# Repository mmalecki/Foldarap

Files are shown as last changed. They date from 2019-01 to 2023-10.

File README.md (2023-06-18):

The Swoon, a folding RepRap
============================

The Swoon is a fork of [Emmanuel Gilloz's Foldarap](https://github.com/EmmanuelG/Foldarap), aimed at upgrading
it with a new motion system based on belts and linear rails, as well as making it compatible with the [EVA 3.0 carriage platform](https://main.eva-3d.page/).

The original SketchUp CAD model has mostly been recreated in [OpenSCAD](https://openscad.org/).

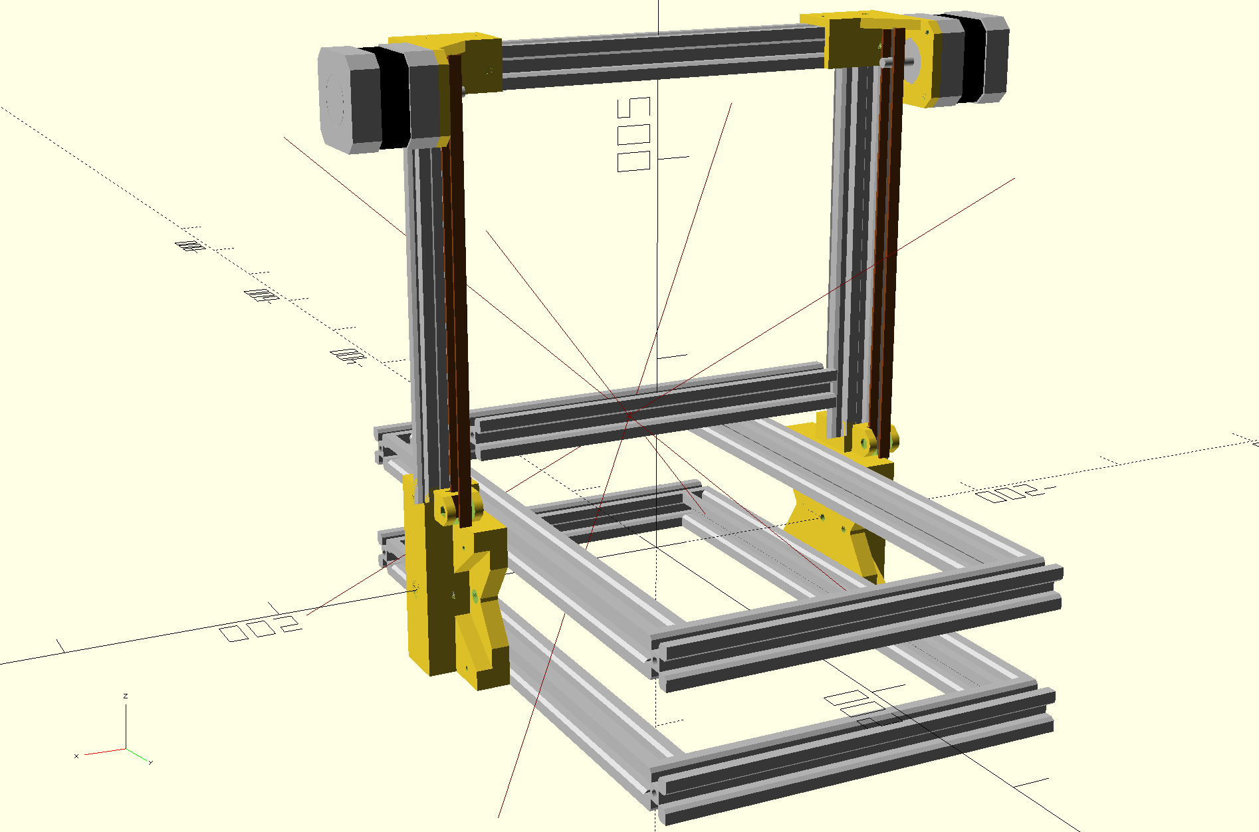
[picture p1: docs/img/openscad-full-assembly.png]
OpenSCAD assembly


This project is still heavily WIP. Belted Z has been implemented, with the rest coming shortly.

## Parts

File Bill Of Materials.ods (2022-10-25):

T (alim ext) | U |  |  | Total | Base |  |  | Y-axis |  |  |  |  | Electronics |  |  | Z-axis |  |  | X-axis |  |  |  |  | Spool roller
662.1 | 473.88 | Exemple Link | Item F 4.0 | 332.6 | Chassis | Hinges | Panels | Y-endstop | Y-idler | Y-slider | Y-motor | Plate | Rear plate | Front plate | Board | Chassis | Z-motor | Handle | Extruder | X-motor | X-endstop | Fan | Hot-end
45 | 25 | Motedis (http://www.motedis.com/shop/Friends-of/FoldaRap-v30/Kit-FoldaRap-v30::5729.html) | V-slot aluminium profile 2020 200mm | 6 | 4 |  |  |  |  |  |  |  |  |  |  | 1 |  |  |  | 1
 |  |  | V-slot aluminium profile 2020 300mm | 6 | 4 |  |  |  |  |  |  |  |  |  |  | 2
 |  |  | M4 T-nut | 62 | 16 | 6 | 4 | 1 | 1 |  | 2 |  | 8 | 4 |  | 10 | 4 | 2 |  | 4
 |  |  | GT2 6mm 600mm timing belt (1m) | 1 |  |  |  |  |  | 1
 |  |  | GT2 20 teeth, 5mm bore timing pulley | 1 |  |  |  |  |  |  | 1
15 | 1 | Kipp (https://www.kipp.fr/fr/fr/Produits/Eléments-de-manœuvre-Eléments-normalisés/Poussoirs-à-ressort-doigt-d-indexage-broches-à-billes/K0334-Poussoirs-à-ressort-mo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) | Ball spring plunger - Kipp K0334.210 | 8 |  | 8
20 | 10 | Fix-n-vis | M3n | 4 |  |  |  |  |  |  |  |  |  |  |  |  | 2 |  |  |  |  |  | 2
 |  | Fix-n-vis | M3n wing | 3 |  |  |  |  |  |  |  | 3
 |  | Fix-n-vis | M3nN | 8 |  |  |  |  | 1 | 4 |  | 3
 |  | Fix-n-vis | M3 washer | 1 |  |  |  |  | 1
 |  | Fix-n-vis | M3x6 headless | 5 |  |  |  |  |  |  |  |  |  |  |  |  |  |  |  | 5
 |  |  | M2.5x12 | 8
 |  | Fix-n-vis | M3x8 CHC | 10 |  |  |  |  |  |  |  |  |  |  | 4 |  | 4 |  |  | 2
 |  | Fix-n-vis | M3x10 CHC | 9 |  |  |  |  |  | 4 | 4 |  |  |  |  |  |  |  | 1
 |  | Fix-n-vis | M3x20 CHC | 1 |  |  |  |  | 1
 |  | Fix-n-vis | M3x25 CHC | 4 |  |  |  |  |  |  |  |  |  |  |  |  |  |  | 4
 |  | Fix-n-vis | M3x30 TFHC | 11 |  |  |  |  |  |  |  | 3 |  |  |  |  | 4 |  |  | 2 |  |  | 2
 |  | Fix-n-vis | M4x8 TBHC | 52 | 16 | 6 | 4 | 1 | 1 |  | 2 |  | 8 |  |  | 10 |  | 2 |  | 2
 |  | Fix-n-vis | M4x10 TBHC | 10 |  |  |  |  |  |  |  |  |  | 4 |  |  | 4 |  |  | 2
 |  | Fix-n-vis | M4x25 CHC | 2 |  | 2
 |  | Fix-n-vis | M4nN | 2 |  | 2
 |  | Fix-n-vis | M4 medium washer | 4 |  | 4
 |  |  | M2.5 heat set insert | 8 |  |  |  |  |  |  |  |  |  |  |  |  |  |  |  |  |  | 8
45 | 30 | e3d (https://e3d-online.com/lite6) | E3D Lite 6 HotEnd | 1 |  |  |  |  |  |  |  |  |  |  |  |  |  |  |  |  |  |  | 1
 |  | e3d (https://e3d-online.com/thermal-compound-paste) | Thermal compound paste | 0
 |  | e3D / RRW / Robotdigg | Filament drive gear (with grub screw) | 1 |  |  |  |  |  |  |  |  |  |  |  |  |  |  | 1
15 | 9 | metalaladecoupe (http://www.metalaladecoupe.com/francais/toles.asp?tbout=alu) | 150 x 140 x 4 mm aluminium plate | 1 |  |  |  |  |  |  |  | 1
30 | 20 | printbite (https://flex3drive.com/product/printbite/) | PrintBite 150 x 140 mm | 1 |  |  |  |  |  |  |  | 1
70 | 0.4 | Robotdigg (https://www.robotdigg.com/product/188/2pin-1M-Long-Thermistor-Cables-w/-Dupont-Connector) | 1 m 2-pin Dupont connector cable | 3 |  |  |  | 1 |  |  |  |  |  |  |  |  |  |  |  |  | 1 | 1
 | 0.6 | Robotdigg (https://www.robotdigg.com/product/141/Endstop-Subminiature-Switch-SS-5GL) | Mechanical endstop switch | 2 |  |  |  | 1 |  |  |  |  |  |  |  |  |  |  |  |  | 1
 | 6.6 | Robotdigg (https://www.robotdigg.com/product/7/NEMA17-40mm-long-17hs3001-20b-Stepper-Motor) | Nema17 – 40mm – 1.20A 4000gr – 50cm (240gr) | 4 |  |  |  |  |  |  | 1 |  |  |  |  |  | 2 |  | 1
 | 6.6 | Robotdigg (https://www.robotdigg.com/product/1034/Nema17-Pancake-Stepper-Motor) | Nema17 – 22mm – 0.8A 1200gr – 80cm (200gr) | 1 |  |  |  |  |  |  |  |  |  |  |  |  |  |  |  | 1
 |  | Robotdigg / Aliexpress | 90 W 100 x 100 m heating film with 100k thermistor and 2 pin molex connector | 1 |  |  |  |  |  |  |  | 1
 | 0.25 | Robotdigg (https://www.robotdigg.com/product/262/Ball-Bearing-603,-604) | 603ZZ bearing | 3 |  |  |  |  | 2 |  |  |  |  |  |  |  |  |  | 1
 | 0.3 | Robotdigg (https://www.robotdigg.com/product/12/608ZZ-Ball-Bearing) | 608ZZ bearing | 4 |  |  |  |  |  |  |  |  |  |  |  |  |  |  |  |  |  |  |  | 4
 |  | Robotdigg (https://www.robotdigg.com/product/249/PC4-01,-PC6-01,-PC4-M4,-PC6-M6-for-Bowden-Extruder) | PC4-B1 pneumatic fitting (4 mm tube, M6 thread) | 1 |  |  |  |  |  |  |  |  |  |  |  |  |  |  | 1
120 | 1.69 | RepRapWorld (https://reprapworld.com/products/cables_and_wiring/wires/heater_wire_yellow_1m_rated_5a/) | 18 AWG cable, green 250 mm | 1 |  |  |  |  |  |  |  |  | 1
 | 1.69 | RepRapWorld (https://reprapworld.com/products/cables_and_wiring/wires/heater_wire_red_1m_rated_5a/) | 18 AWG cable, red 250 + 100 mm | 1 |  |  |  |  |  |  |  |  | 1
 | 1.69 | RepRapWorld (https://reprapworld.com/products/cables_and_wiring/wires/heater_wire_black_1m_rated_5a/) | 18 AWG cable, black 250 + 100 mm | 1 |  |  |  |  |  |  |  |  | 1
 | 60 | RepRapWorld (https://reprapworld.com/products/electronics/minitronics/minitronics_v1_1_basic_kit/) | Minitronics + molex cable | 1 |  |  |  |  |  |  |  |  |  |  | 1
 | 5 | RepRapWorld (https://reprapworld.com/products/cables_and_wiring/wires/power_cable_1_8m/) | EU power cord | 1 |  |  |  |  |  |  |  |  | 1
 | 40 | RepRapWorld (https://reprapworld.fr/products/_lectronique/impression_autonome/_cran_graphique_lcd_v1_0/) | LCD écran pour Minitronics | 1 |  |  |  |  |  |  |  |  |  |  | 1
 | 2 | RepRapWorld (https://reprapworld.com/products/cables_and_wiring/cable_binding/cable_wrapping_10mm_1_meter/) | 1 m cable spiral wrap | 1.6 |  |  |  |  |  |  |  |  |  |  |  |  | 0.8 |  |  |  |  |  | 0.8
 | 3 | RepRapWorld (https://reprapworld.com/products/electronics/minitronics/usb_connection_cable_0_5m_type_b_to_type_a/) | USB cable | 1 |  |  |  |  |  |  |  |  |  |  | 1
 | 1.5 | RepRapWorld (https://reprapworld.com/products/cables_and_wiring/heatshrink/heatshrink_black_20cm_1_6mm_bore_0_8mm_shrunken/) | Heat shrink sleeve for the fans
40 | 1.32 | RS (http://fr.rs-online.com/web/p/products/0178462) | Zip ties | 7 |  |  |  |  |  | 5 |  |  |  | 2
 |  | RS (http://fr.rs-online.com/web/p/clips-de-maintient-de-cables/1705346/) | Cable clip 25x25x8m | 1 |  |  |  |  |  |  |  |  |  |  |  |  |  |  | 1
 | 1.72 | RS (http://fr.rs-online.com/web/p/gaine-thermoretractable-avec-adhesif/1706361/) | Heat shrink sleeve 1.6-0.8 mm 20 mm | 2 |  |  |  |  |  |  |  |  |  |  |  |  |  |  |  |  |  | 2
 | 0.03 | RS (http://fr.rs-online.com/web/p/embouts-de-cablage-a-sertir/2114268/) | Ferrule for the fans | 2 |  |  |  |  |  |  |  |  |  |  |  |  |  |  |  |  |  | 2
 | 1.89 | RS (http://fr.rs-online.com/web/p/gaine-thermoretractable-avec-adhesif/1706399/) | Heat shrink 4.8-2.4mm 20 mm | 4 |  |  |  | 2 |  |  |  |  |  |  |  |  |  |  |  |  | 2
 | 0.5 | RS (https://www.rs-particuliers.com/web/p/ressorts-de-compression/751483/) | 751-483 compression spring | 5 |  |  |  |  |  |  |  | 3 |  |  |  |  |  |  | 2
15 | 15 | Aliexpress / RS (https://fr.aliexpress.com/store/product/2-Pieces-Gdstime-12V-2Pin-3cm-30mm-x-30mm-x-10mm-Ball-Bearing-Brushless-DC-Cooling/212707_32797692869.html) | 30 x 30 x 10 mm fan (4.7 CFM) | 2 |  |  |  |  |  |  |  |  |  |  |  |  |  |  |  |  |  | 2
 |  | mouser (60) (https://www.mouser.fr/ProductDetail/MEAN-WELL/GST160A12-R7B/) | Meanwell 12 V 138 W (OEM / or not EU) external power supply
115 | 115 | RS (https://rs-particuliers.com/Product.aspx?Product=1176149) | Meanwell 12 V 138 W external power supply | 1 |  |  |  |  |  |  |  |  | 1
 |  | mouser (60) (https://www.mouser.fr/search/ProductDetail.aspx?R=0virtualkey0virtualkeyGST160A24-R7B) | Meanwell 24 V 160W (OEM / or not EU) external power supply
 |  | RS ? | Meanwell 24 V 160W external power supply
 |  | mouser (3) (https://www.mouser.fr/ProductDetail/Kycon/KPJX-PM-4S) | KPJX-PM-4S connector
7 | 7 | RS (https://rs-particuliers.com/Product.aspx?Product=6677287) | KPJX-PM-4S connector | 1 |  |  |  |  |  |  |  |  | 1
 |  | mouser (9) (https://www.mouser.fr/ProductDetail/Kycon/KPJX-PM-4S-S) | 8 mm drill or 90° reamer (alu plate)
0.1 | 0.1 | Fix-n-vis | M2.5x10 for plastic (? - play compensation ?) | 2 |  |  |  |  |  |  |  |  | 2
85 | 75 |  | PIECES 3D – PLA
 |  | silver | face-panel-A | 1 |  |  |  |  |  |  |  |  | 1
 |  | silver | face-panel-B-psu-external | 1 |  |  |  |  |  |  |  |  | 1
 |  | silver | side-panel-A | 2 |  |  | 2
 |  | navy | x-slider | 1 |  |  |  |  |  |  |  |  |  |  |  |  |  |  |  | 1
 |  | silver | y-carriage | 1 |  |  |  |  |  |  |  | 1
 |  | navy | y-slider-R | 1 |  |  |  |  |  | 1
 |  | navy | y-slider-L | 1 |  |  |  |  |  | 1
 |  | navy | z-slider-R | 1 |  |  |  |  |  |  |  |  |  |  |  | 1
 |  | navy | z-slider-L | 1 |  |  |  |  |  |  |  |  |  |  |  | 1
 |  | navy | hinge-outer | 2 |  | 2
 |  | navy | hinge-inner | 2 |  | 2
 |  | silver | extruder-body | 1 |  |  |  |  |  |  |  |  |  |  |  |  |  |  | 1
 |  | silver | extruder-lever | 1 |  |  |  |  |  |  |  |  |  |  |  |  |  |  | 1
 |  | silver | board-mount_minitronics | 2 |  |  |  |  |  |  |  |  |  |  | 2
 |  | silver | foot-A | 2 | 2
 |  | silver | foot-B | 2 | 2
 |  | silver | pinion | 3 |  |  |  |  |  |  |  |  |  |  |  |  | 2 |  |  | 1
 |  | orange | handle | 1 |  |  |  |  |  |  |  |  |  |  |  |  |  | 1
 |  | silver | top-corner | 2 |  |  |  |  |  |  |  |  |  |  |  | 2
 |  | navy | spool-roller | 2 |  |  |  |  |  |  |  |  |  |  |  |  |  |  |  |  |  |  |  | 2
 |  | silver | spool-roller tube | 2 |  |  |  |  |  |  |  |  |  |  |  |  |  |  |  |  |  |  |  | 2
 |  | silver | y-endstop-holder | 1 |  |  |  | 1
 |  | silver | x-rack | 1 |  |  |  |  |  |  |  |  |  |  |  |  |  |  |  | 1
 |  | silver | z-rack | 2 |  |  |  |  |  |  |  |  |  |  |  |  | 2
 |  | navy | rack-end | 6 |  |  |  |  |  |  |  |  |  |  |  |  | 4 |  |  | 2
 |  | silver | y-motor | 1 |  |  |  |  |  |  | 1
 |  | silver | y-idler | 1 |  |  |  |  | 1
 |  | orange | e3d-lite6 | 1 |  |  |  |  |  |  |  |  |  |  |  |  |  |  |  |  |  |  | 1
 |  | orange | e3d-lite6-30mmfanshroud | 1 |  |  |  |  |  |  |  |  |  |  |  |  |  |  |  |  |  |  | 1
 |  | silver | lcd-clip | 1 |  |  |  |  |  |  |  |  |  |  | 1
40 | 30 |  | PIECES DECOUPEES
 |  |  | Underplate – 4 mm PMMA | 1 |  |  |  |  |  |  |  |  |  | 1
 |  |  | Outils nécessaires
 |  | Fix-n-vis | 1.5 mm Allen key (STHC M3) | 1
 |  | Fix-n-vis | 2.0 mm Allen key (TFHC M3) | 1
 |  | Fix-n-vis | 2.5 mm Allen key (CHC M3, TBHC M4) | 1
 |  | Fix-n-vis | 3.0 mm Allen key (CHC M4) | 1
 |  | e3D / RS / Robotdigg | 7.0 mm wrench (M4 nuts, e3D nozzle) | 1
 |  | RS (https://rs-particuliers.com/WebCatalog/Coupe_fil_Encastre__longueur_138mm__capacite_de_coupe_13mm-2450491.aspx) | Flat-nose pliers | 1
 |  |  | Options
 |  |  | Tweezers | 1
 |  |  | Flat file | 1
 |  |  | 8 mm drill or 90° reamer (alu plate)
 |  | RepRapWorld (https://reprapworld.com/products/cables_and_wiring/wires/connector_cable_for_stepper_motor_30cm_4_leads/) | Stepper cable 30cm JST / Molex (Y)
 |  | Robotdigg (https://www.robotdigg.com/product/192/One-end-Dupont-connector-for-RDG-Stepper-Motors) | Stepper cable 30-50-80cm JST / Dupont (Y/E/Z)
 | 7.2 | Robotdigg (https://www.robotdigg.com/product/1250/42HM34-0.9-step-angle-NEMA17-stepper-motor) | Nema17 – 40mm – 1.68A xx00gr – 09° (for E ?) (2x0gr)
 | 6.6 | Robotdigg (https://www.robotdigg.com/product/7/NEMA17-40mm-long-17hs3001-20b-Stepper-Motor) | Nema17 – 40mm – 1.20A 4000gr – 50cm (240gr)
 |  | 16 | silver
 |  | 9 | navy
 |  | 3 | orange

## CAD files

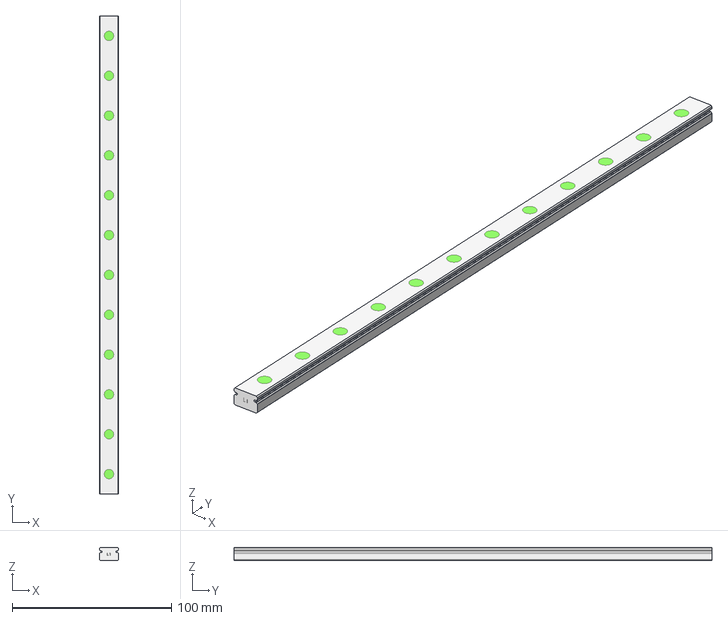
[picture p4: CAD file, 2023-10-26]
cad/vitamins/MGNR12R300HM_FILE_1.stp
12.0 x 300.0 x 8.00 mm

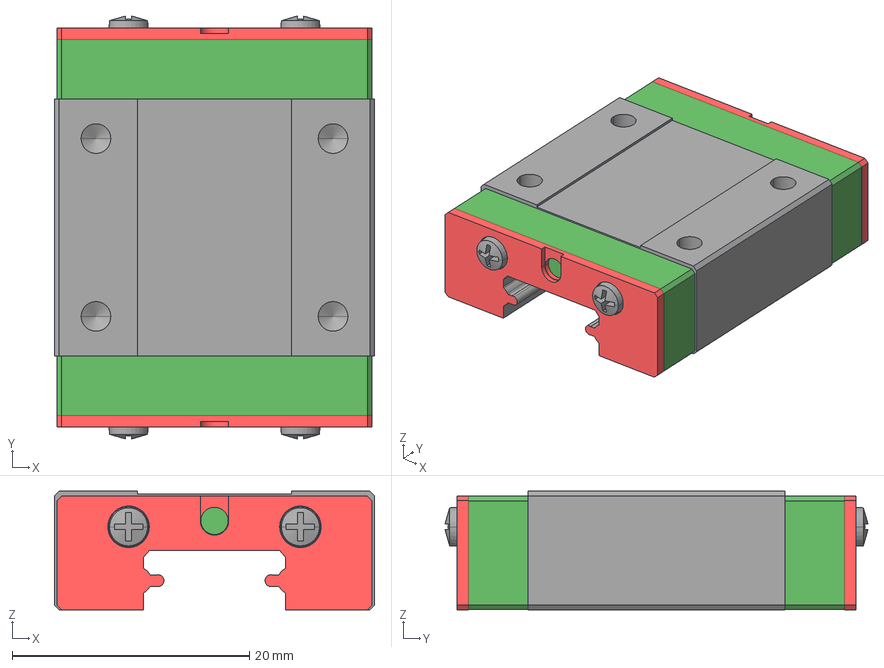
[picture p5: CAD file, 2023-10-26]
cad/vitamins/MGN12CZ0HM_FILE_2.stp
27.0 x 35.7 x 10.0 mm

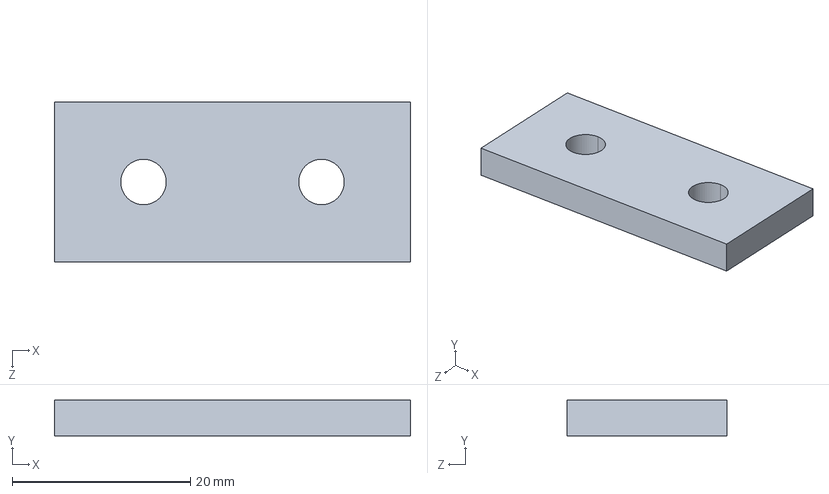
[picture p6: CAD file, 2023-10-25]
cad/vitamins/Joining Strip Plate 2 Hole.step
40.0 x 4.00 x 18.0 mm

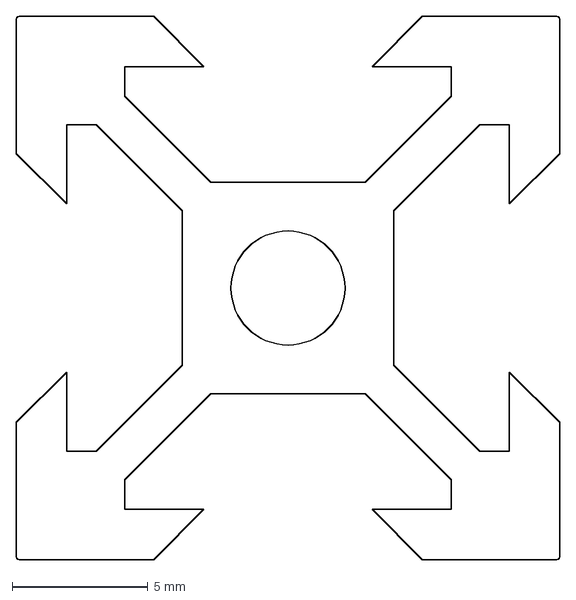
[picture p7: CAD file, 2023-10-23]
cad/vitamins/vslot-2020_1.dxf
20.0 x 20.0 mm

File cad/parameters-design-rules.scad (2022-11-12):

use <catchnhole/catchnhole.scad>;

press_fit = 0;
v_slot_sliding_fit = 0.021; // H7/h6 over a 20 mm "shaft"
tight_fit = 0.1;
fit = 0.2;
loose_fit = 0.5;

// Thickness of a wall holding onto aluminium extrusion.
v_slot_wall_t = 4;
// And a length of the bolt going through said wall, and into a t-nut
// in the extrusion.
v_slot_wall_t_bolt_l = 8;

// Thickness of a wall holding onto a belt.
belt_wall_t = 2;

// Thickness of a wall holding a stepper.
stepper_mount_plate_t = 5;
// How much of a bolt should go into a stepper at minimum.
stepper_bolt_l = 4;

bolt = "M3";
// Minimal amount of material around a bolt hole for our standard bolt (M3):
bolt_wall_d = 7;
// Minimal height of a bolt hole for our standard bolt (M3):
bolt_wall_h = 3;
// Minimal amount of material around a nut for our standard bolt (M3):
nut_wall_d = 9;
nut_wall_h = nut_height(bolt) + 2/3 * bolt_wall_h;

// The bolt size we're going to use to put the frame together:
frame_bolt = "M4";
frame_bolt_wall_d = 7.5;

// And here's the bolt you could tap into the end of extrusions, if so inclined.
frame_tap_bolt = "M5";

endstop_wall_t = 1.6;
endstop_fit = fit;

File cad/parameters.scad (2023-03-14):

$fn = 200;

include <parameters-design-rules.scad>;
include <vitamins/gt2-parameters.scad>;
include <vitamins/nema17-parameters.scad>;
include <vitamins/v-slot-parameters.scad>;

x_carriage_bolt_s = 25;

y_carriage_slider_bolt = "M3";
y_carriage_slider_bolt_d = "M3";

y_carriage_slider_l = 140;
y_carriage_slider_w0 = 68;
y_carriage_slider_w1 = 80;

// Measured in CAD:
v6_hotend_mount_w = 35;
v6_hotend_mount_h = 12;
v6_hotend_mount_l = 11.5;

x_v_slot_l = 200;
y_v_slot_l = 300;
z_v_slot_l = 300;

bed_w = 150;
bed_l = 140;

// Measured on the outer hinge component in CAD, very important to keep consistent,
// otherwise you skew the Z extrusions one way or the other.
frame_z_x_offset = 7;
// Offset between the outside edge of the Y- X extrusion and the
// edge of the Z extrusion.
frame_z_y_offset = 130;

// Distance between the outer edges of the Y extrusions in the Z axis.
frame_y_z_offset = 80;

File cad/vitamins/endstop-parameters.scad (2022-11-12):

endstop_w = 6.2;
endstop_l = 20;
endstop_h = 10.2;
endstop_connector_w = 8.4;
endstop_ridge = 0.5;

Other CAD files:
cad/vitamins/gt2-parameters.scad
cad/assemblies/frame.scad
cad/assemblies/full.scad
cad/assemblies/top-corner.scad
cad/assemblies/x-axis.scad
cad/assemblies/z-axis-left.scad
cad/assemblies/z-axis-right.scad
cad/assemblies/z-axis.scad
cad/e3Dv6-mount.scad
cad/gt2-tensioner-clamp.scad
cad/hinge-outer.scad
cad/sizing.scad
cad/top-corner.scad
cad/vitamins/endstop.scad
cad/vitamins/gt2.scad
cad/vitamins/mgn12-parameters.scad
cad/vitamins/mgn12.scad
cad/vitamins/nema17-parameters.scad
cad/vitamins/nema17.scad
cad/vitamins/v-slot-parameters.scad
cad/vitamins/v-slot.scad
cad/x-carriage.scad
cad/z-gantry-left.scad
cad/z-gantry-right.scad
cad/z-gantry.scad
cad/z-idler.scad

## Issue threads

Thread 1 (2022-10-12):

Add optional centering bolts and nutcatches on the outer and inner hinges

mmalecki, 2022-10-12:

mmalecki, 2022-11-12:
We've got these going on the outer hinges, but let's punt the inner until the EVA milestone. The structure is fairly rigid after #3 and #7 landed.

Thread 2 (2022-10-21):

Remove backlash in Z axis

mmalecki, 2022-10-21:
The current rack and pinion system presents considerable backlash (~0.6 mm).

While it could definitely be tweaked, possibly by either:
* pressing the pinion harder into the rack
* software backlash compensation (albeit unavailable in Duet)
* just using Foldarap as intended (Z moved to 0 by hand in between prints, and only going up during the print)

I'd like to modernize this machine a little, and a stable Z axis is a must.

Therefore, the action required here is changing out the Z motion system.

# Drive options
There are 2 possible drives here:

## Leadscrews
Pros:
* small, precise steps out of the box

Cons:
* built-in grooves for dirt (may be challenging in a traveling environment)
* tricky placement in current design (or is it?)

## Belts
Pros:
* cheap
* can get down to 5 micron steps with 16t pulley and microstepping with no gearbox
* fit neatly into current design (and Emmanuel has tried them before)

Cons:
* tensioning
* the gantry may drop on power loss

# Linear guides
And few possible linear guides:
* keeping the 3D printed guides on aluminium extrusions
* linear rods - possible, but mounting would be tricky
* linear rails mounted to aluminium extrusions
* V-slot trolleys or Exoslides - both would be tricky to fit into Z axis with the space constraints

Linear rails, oddly enough, come up as the most compact solution. Linear rods require another, seperate part of the carriage and a LMU bearing, while V-slot trollers or Exoslides extend our carriages in all the dimensions. MGN12 it is.
May keep the 3D printed guides as an option, albeit with better fits (H7).

mmalecki, 2022-11-12:
This is more or less done. I say more or less, because it won't be fully complete until we solve #11, but it's how far we'll get for the time being.

Closed 2022-11-12.

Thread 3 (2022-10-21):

Fix outer hinge plunger dimensions

mmalecki, 2022-10-21:
The plunger, as listed in BOM, has different dimensions than those in CAD.

Closed 2022-11-12.

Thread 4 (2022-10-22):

Fix Z axis skew caused by different extrusion spacing

mmalecki, 2022-10-22:
The Z axis extrusions slop "inside" the structure, due to different spacing at the bottom outer hinge = 7 mm and the top corner joint = 6 mm.

Closed 2022-11-12.

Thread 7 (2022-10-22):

Place the plunger tips at ends of fit zones

mmalecki, 2022-10-22:
Unsurprisingly, the plungers don't fit the v-slot extrusions exactly. At their relaxed state, the part we're interfacing d = 7.5 mm, while the channel is w = 8.5 mm. We can place the plungers not at the center of the channel as currently, but slightly off-center, so they interface with the channel directly instead of leaving 1 mm of clearance.

Closed 2022-11-12.

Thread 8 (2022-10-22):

Fix the Z probe XY offset

mmalecki, 2022-10-22:
I just realized it's wrong.

mmalecki, 2022-11-12:
Maths is hard, but ours seems to check out.

Closed 2022-11-12.

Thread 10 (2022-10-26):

Linear rail on Y axis

mmalecki, 2022-10-26:
Two of them, most likely. Current sliders have a fair amount of play.

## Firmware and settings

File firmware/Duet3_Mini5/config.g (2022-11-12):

; Configuration file for Duet 3 Mini 5+ (firmware version 3.3)
; executed by the firmware on start-up
;
; generated by RepRapFirmware Configuration Tool v3.3.10 on Fri Mar 25 2022 23:49:05 GMT+0100 (Central European Standard Time)

; General preferences
M575 P1 S1 B57600                        ; enable support for PanelDue
G90                                      ; send absolute coordinates...
M83                                      ; ...but relative extruder moves
M550 P"FoldaRap"                         ; set printer name

; Network
M552 S1                                  ; enable network
M586 P0 S1                               ; enable HTTP
M586 P1 S0                               ; disable FTP
M586 P2 S0                               ; disable Telnet

M669 K0                                  ; Cartesian kinematics

; Drives
M569 P0 S0                               ; physical drive 0 goes backwards X
M569 P1 S0                               ; physical drive 1 goes backwards Y
M569 P2 S0                               ; physical drive 2 goes backwards Z-left
M569 P3 S1                               ; physical drive 3 goes backwards Z-right
M569 P4 S1                               ; physical drive 3 goes backwards E
M584 X0 Y1 Z2:3 E4                       ; set drive mapping
M350 X32 Y32 Z32 E32 I1                  ; configure microstepping
M92 X152.50 Y160.80 Z200.00 E800.00      ; set steps per mm
M566 X600.00 Y600.00 Z60 E600.00         ; set maximum instantaneous speed changes (mm/min)
M203 X6000.00 Y6000.00 Z600 E3000.00     ; set maximum speeds (mm/min)
M201 X600.00 Y600.00 Z150 E1000.00       ; set accelerations (mm/s^2)
M906 X800 Y1200 Z1750 E575               ; set motor currents (mA)
M84 S0                                   ; Disable motor idle current reduction

; Axis Limits
M208 X0 Y0 Z0 S1                         ; set axis minima
M208 X142 Y145 Z142 S0                   ; set axis maxima

; Endstops
M574 X1 S1 P"io5.in"                     ; configure switch-type (e.g. microswitch) endstop for low end on X via pin io5.in
M574 Y1 S1 P"io6.in"                     ; configure switch-type (e.g. microswitch) endstop for low end on Y via pin io6.in

; Z-Probe
M950 S0 C"io1.out"
M558 P9 C"io1.in" H5 F120 T6000
G31 X-17.244 Y-20.75 Z3.3 P25            ; define probe offsets
M574 Z1 S2                               ; use the z-probe as z endstop
M402                                     ; stow the probe on startup

M557 X20:120 Y30:120 S15
M376 H2
M671 X-42:184 Y0:0

; Heaters
M308 S0 P"temp0" Y"thermistor" T100000 B3950   ; the bed thermistor as sensor 0
M950 H0 C"out0" T0
M307 H0 B0 S1.00
M140 H0
M143 H0 S120

M308 S1 P"temp1" Y"thermistor" T100000 B4725 C7.06e-8 ; the hot-end thermistor as sensor 1
M950 H1 C"out1" T1                                    ; create a hot-end heater on out1
M307 H1 B0 S1.00                                      ; disable bang-bang mode for heater  and set PWM limit
M143 H1 S280                                          ; set temperature limit for heater 1 to 280C

; Fans
M950 F0 C"out5" Q100 ; the print fan
M106 P0 S0 H-1

M950 F1 C"out6" Q100 ; the hot-end fan
M106 P1 S0 H1 T45    ; thermostatic control for the hot-end fan, using sensor 1

; Tools
M563 P0 D0 H1 F0                                      ; define tool 0
G10 P0 X0 Y0 Z0                                       ; set tool 0 axis offsets
G10 P0 R0 S0
T0

; Pressure advance
M572 D0 S0.1 ; value picked according to https://docs.duet3d.com/en/User_manual/Tuning/Pressure_advance

; Custom settings are not defined
M501         ; load config-override.g

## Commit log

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2019-01-22 clip for lcd screen
    [Bill Of Materials.ods, lcd-clip.stl]
2019-01-27 adding an LCD screen
    [Bill Of Materials.ods]
2019-01-27 step/mm for 0.9° motor in Z
    [Configuration.h]
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2022-09-27 Export the actual inner hinge from CAD
    [hinge-inner 2off.stl]
2022-10-09 Generate the initial Duet3 Mini5 configuration
    [config.g]
2022-10-09 Move the endstops to 3-pin connectors
    [config.g]
2022-10-09 My wiring is backwards, oh well
    [config.g]
2022-10-09 Set steps per mm for 1.8 steppers
    [config.g]
2022-10-09 Set motor currents as for BOM motors
    [config.g]
2022-10-09 Configure a bed temp thermistor
    [config.g]
2022-10-11 Increase maximum Z current to 120 % stepper rating
    The duty factor for these motors is low.
    [config.g]
2022-10-12 Hook up the hot-end and bed heaters, add a tool
    [config.g]
2022-10-12 Up the Z motor current to 125 % of rating
    [config.g]
2022-10-16 Pick the right fan for the tool
    Select tool 0.
    [config.g]
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2022-10-16 Add a support-less fan shroud
    Let users make their own support decisions.
    [e3Dlite6_30mmfanshroud 1off.stl]
2022-10-16 Add a BLTouch 3.1 mount, the very first iteration
    [e3Dv6-bltouch-mount.scad, e3Dv6-mount.scad, parameters-design-rules.scad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]
2022-10-17 Correct tolerances and fits after v1
    [e3Dv6-bltouch-mount.scad]
2022-10-17 Explain the design rules
    [parameters-design-rules.scad]
2022-10-20 Add BLTouch Duet configuration
    [config.g]
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2022-11-01 Add a functional, non-skewed top corner
    Fix #4.
    [e3Dv6-bltouch-mount.scad, parameters-design-rules.scad, parameters-v-slot.scad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]
2022-11-01 Add a stepper mount to the top corner
    [nema17.scad, parameters-design-rules.scad, parameters-nema17.scad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]
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2022-11-01 Start implementing Z gantries
    Beef up the stepper mount, it's a bit wobbly with just 4 mm.
    Give the belt and gantries more space.
    More mock in the mockup.
    [gt2.scad, mgn12.scad, mockup.scad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]
2022-11-01 Add the spacing between top and bottom frame extrusion
    [parameters.scad]
2022-11-01 Use `v_slot_mockup`
    Move the mock X axis to its right place.
    [mockup.scad]
2022-11-01 Hold less of the X axis on the Z gantry
    It collided with the rack.
    [z-gantry-right.scad]
2022-11-01 Add a initial implementation of the outer hinge
    Fixes #7. Fixes #3.
    [hinge-outer.scad, parameters-v-slot.scad]
2022-11-01 Add a part file for the GT2 tensioner clamp itself
    [gt2-tensioner-clamp.scad]
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2022-11-01 Use design rules to derive proper z-idler wall thickness
    [v-slot.scad, z-idler.scad]
2022-11-01 Leave side clearance for the bolt holding X axis
    [z-gantry-right.scad]
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2022-11-01 Fix a missing `use`
    [z-gantry-left.scad]
2022-11-01 Break out the vitamins into a separate directory
    [gt2-parameters.scad, gt2-tensioner-clamp.scad, gt2.scad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]
2022-11-01 Only move to 95 % of calculated end of fit offset
    The plungers beg for quick death with every folding otherwise.
    [hinge-outer.scad]
2022-11-01 Looser fit on plunger flange
    [hinge-outer.scad]
2022-11-01 Make the plunger access hole smaller
    And lower. The plungers have a access hole themselves, leading straight
    to the spring.
    [hinge-outer.scad]
2022-11-01 Move the GT2 tensioner clamp to a separate file
    [gt2-tensioner-clamp.scad, gt2.scad]
2022-11-01 Base the idler height upon the idler gear height
    Use 16t idlers for the Z axis. We've previously left clearance for 20t,
    but space is precious in the Z-zone. Additionally, these increase our
    resolution.
    [gt2-parameters.scad, z-idler.scad]
2022-11-01 Use real GT2 belt thickness in the mockup
    [mockup.scad]
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2022-11-01 Rotate the belt clamp in the Z gantry, get some more belt holding in
    [z-gantry.scad]
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2022-11-01 Add clearance for the Z idler on the outer hinge
    [hinge-outer.scad]
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2022-11-01 Correct the Z gantry mating with X axis
    Tweak angles and belts.
    [z-gantry.scad]
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2022-11-01 Add a safety margin to the idler nut wall diameter
    [z-idler.scad]
2022-11-01 Add a third bolt, in the back of the z-idler
    [z-idler.scad]
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2022-11-01 Move the sliders to the side to mate better
    [v-slot.scad]
2022-11-01 Fix 45 degree support in Z idler
    [z-idler.scad]
2022-11-01 Add a LGX extruder mount to the left Z gantry
    [z-gantry-left.scad]
2022-11-01 Fix the X extrusion spacing in Z gantry
    [z-gantry.scad]
2022-11-01 Stop extending the X holding part by X-Z frame offset
    It's too much because this offset is already included earlier.
    [z-gantry.scad]
2022-11-01 Add endstop mounting to the left Z gantry
    [endstop-parameters.scad, endstop.scad, parameters-design-rules.scad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]
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2022-11-01 Loosen the plunger-v-slot fit a little
    [hinge-outer.scad]
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2022-11-01 Increase the clearance for the endstop connector
    [endstop-parameters.scad]
2022-11-01 Fix extrusion frame spacing
    [frame.scad]
2022-11-01 Set Z idler clearance to 0
    [hinge-outer.scad]
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2022-11-01 Fix fits around the plungers
    [hinge-outer.scad]
2022-11-01 Change where the X-Z offset happens in the gantry
    [z-gantry.scad]
2022-11-01 Fix positioning in the full assembly
    [full.scad, parameters.scad, z-axis.scad]
2022-11-01 Fix clearances around the Z stepper mount
    Include the mount in the positive. Clear out the full length of
    extrusion, instead of only what we're holding onto.
    [top-corner.scad]
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2022-11-01 Configure Z probe as Z endstop
    Fixes #9.
    [config.g]
2022-11-01 Move the endstop to the end of axis hold, where it belongs
    Move the extruder closer.
    [z-gantry-left.scad]
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2022-11-01 Shorten the Bowden tube a little
    [config.g]
2022-11-01 Add chamfer to NEMA17 mount, use in top corner
    [nema17-parameters.scad, nema17.scad, top-corner.scad]
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2022-11-12 Remove the e-steps per mm
    We use a different extruder now.
    [e-step-per-mm.ods]
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2022-11-17 Make the top corner parametetric with regards to belt location
    [top-corner.scad]
2022-11-17 Fix top-level Z axis assembly call
    [z-axis.scad]
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2022-11-18 Move the v-slot mockup to vitamin file
    Mockup NEMA17s.
    [common.scad, nema17-parameters.scad, nema17.scad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]
2022-11-19 Make the Z idler parametric with regard to belt side
    Change belt mockup to the proper shape.
    [common.scad, gt2.scad, z-axis.scad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]
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2023-03-13 Inset the Z stepper more
    Up to the spindle plate.
    Countersink the extrusion-most bolt.
    [top-corner.scad]
2023-03-14 Add a MGN12 rail to the Z axis
    Stop accepting the gantry as a child - we'll draw it all as X axis
    assembly.
    [z-axis.scad]
2023-03-14 Fix top axis assembly position
    [full.scad]
2023-03-14 Add a vitamin file with MGN12 carriage and rail
    [mgn12.scad]
2023-03-14 Prefix frame offset variables with `frame_`
    Rename some more appropriately.
    [frame.scad, full.scad, hinge-outer.scad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]
2023-03-14 Add a missing top corner assembly
    [top-corner.scad]
2023-04-29 Reformat, show the frame assembly in the assembly file
    [frame.scad]
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2023-05-01 Remove the pen holder
    The pen holder was compatible with the Foldarap tool holder.
    [pen-holder.scad]
2023-05-01 Remove the E3D v6 extruder BLTouch mount
    Again, incompatible with EVA.
    [e3Dv6-bltouch-mount.scad]
2023-05-01 Add `mgn12_mockup`
    Place the MGN12C origin in center.
    [mgn12.scad]
2023-06-18 Remove the STLs from the repository
    We will be using proper release practices from now on.
    [OpenEdge-v2 1off.stl, board-mount_Duet_2off.stl, board-mount_minitronic 2off.stl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]
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2023-10-15 Remove the old rack and pinion, fan airflow calculations
    [CFD-30mm-fan-ducting.FCStd, CFD-30mm-fan-ducting.STEP, parametric_involute_gear_v5.0.scad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]
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2023-10-25 Add missing vitamins
    [Joining Strip Plate 2 Hole.step]
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2023-12-21 Fix the long-standing TODOs in assembly
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
